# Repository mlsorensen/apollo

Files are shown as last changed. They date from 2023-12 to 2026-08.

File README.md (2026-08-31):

#

This project is archived, see [Apollo2](https://github.com/mlsorensen/Apollo2)

# Apollo for LM Micra/Acaia Lunar

Apollo helps land espresso on your Lunar scale. This project adds brew-by-weight and a small controller 
for La Marzocco Micra with Acaia Lunar. It may also work with other Acaia Bluetooth scales like Pyxis. 

This project is more about scale integration than Micra integration. It cannot do flow profiling or other advanced 
control over the Micra, it is simply collecting data from the scale and acting as a proxy for the paddle switch.

**This is a hobby project, as such there is no support.** It is sort of a hack/proof of concept being beaten into shape.
Contributions are welcome, though this is very much designed to work according to my needs, for customization I'd 
suggest forking and making it your own.

# UPDATES

## Umbra support
I've added support for the Acaia Umbra scale, which is very similar to the Lunar scale, but it lacks a display and onboard
controls. This is ideal for integrations. Aside from being much less expensive. it is a bonus not to have to deal with 
accidentally touching controls. The full blank slab is also nice aesthetically.  Additionally, it has a "sleep" mode. This 
enables Apollo to just connect to the scale when needed, and the scale will go to sleep when disconnected - you don't need 
to touch the scale at all except occasionally to charge or clean it!

To accomodate this I've made one fundamental adjustment. I've comandeered the "target lock" toggle switch to become a 
"connect" button. In over a year I never used this button anyway. When depressed, it will connect to the scale and turn 
on the screen. When disabled it will disconnect and the screen will turn off. For a regular Lunar scale, simply leave the 
toggle depressed and you can continue to manage the system by turning on/off the Lunar as before.

## Horizontal display
This is a part of an effort to build a nicer enclosure, building the device into the top panel of the Micra. All of the
wiring and setup below still applies, with the exception of printing a new top panel and using 8mm push switches in place
of the toggle switch to select target weight.

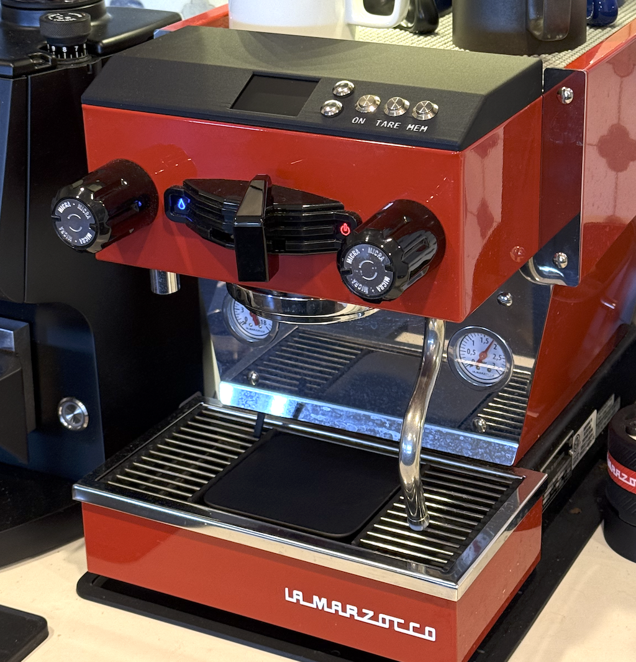
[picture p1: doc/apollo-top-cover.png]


The "Apollo top cover" 3d printing models are in the doc folder.

In my setup I migrated from the Pi Zero 2W to the Raspberry Pi 5, which is overkill CPU-wise and I actually underclock to
1600MHz, but it gives smoother frame rates. I'm sure a Pi 4 or 3 would work too. I use the lite Raspbian image since we 
don't need a full GUI. I insulate the back of the device with tape and tuck it in the open space on the right near the 
steam wand.

I have monitored temperatures closely and not experienced a high enough temperature to throttle the Pi while installed. 
Consider printing the top cover in something more heat resistant like ABS or ASA. I printed in PLA Carbon Fiber for a 
nice texture, rated to withstand 55C, and I've coated the bottom inside shell with a thin layer of neoprene foam. So far 
I haven't seen the top exceed 42C.

I have replaced the top cover screws with M4-0.7 screws made of non-stainless and added 10mm magnets into the top
cover to hold it in place without visible fasteners.

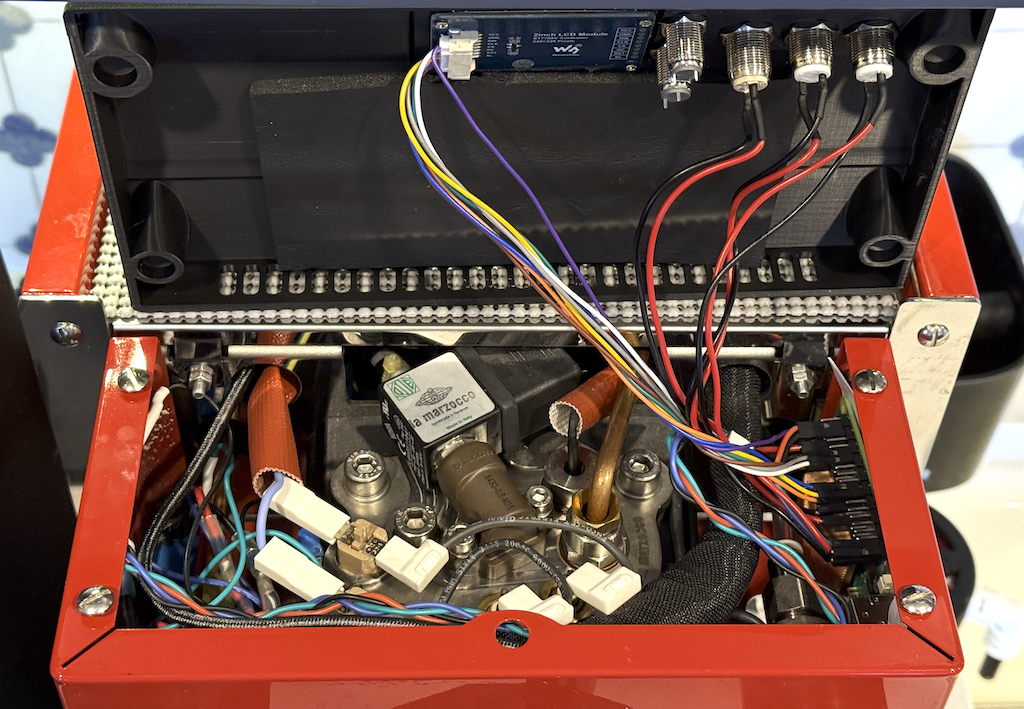
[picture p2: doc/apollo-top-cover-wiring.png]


## Configuration variables
There are some new variables to control framerates and display orientation at `/etc/default/apollo`, documented in the
comments of this file (aka `service/env` in this repo).

## Hardware

### Materials

Note that where external links are provided, they may not age well.

* A Raspberry Pi Zero 2W w/soldered header
* 5v relay w/3.3v compatible logic control
* 5v 2a power supply
* 2.1mm barrel jack connector/wiring harness
* pushbutton switch x 2
* toggle switch
* up/down rocker switch (or two pushbutton switches)
* 2" WaveShare 240x320 SPI display (or compatible)
* Screws - M2.0, M2.5 4mm length, or #3-24 in 1/4" length depending on your 3d printer tolerances
* Silicone 24AWG hook up wire
* Soldering tool and/or 2.54mm crimping set
* 3d printed enclosure, or self-provided alternative

### Controller

A Raspberry Pi was selected to accommodate easy adoption of existing Python libraries without having to
rework them to function on a microcontroller.  Ultimately this is more flexible in terms of expanding
functionality as well.

### Display

The software should support either the [WaveShare 2.0" display](https://www.waveshare.com/2inch-lcd-module.htm) 
or the [2.4" display](https://www.waveshare.com/2.4inch-lcd-module.htm). The 2.4" display seems to have worse
viewing angles and is less sharp, and display_size needs to be updated in `main()`. **For compatibility with the included enclosure, the 2" display should be used.**

### Relay

There isn't one specific relay to link to. Any 5v Arduino/Pi/ESP32 type relay should work. It will have 
common/NC/NO connections on the relay side and 5v/gnd/control pin on the controller side.

### Buttons

I use a momentary pushbutton switch for the tare and memory buttons, a toggle switch for the "scale connect" button,
and an up/down rocker switch for adjusting the target. The up/down rocker switch can be thought of as two momentary
switches with a common ground - you can use two separate buttons as well.

For compatibility with the included 3d printed enclosure, the buttons should be 12mm. The rocker switch should be
rectangular and support 19mm x 13mm opening. 

I found the quality of rocker switches a bit difficult, some had significant bounce leading to them being a bit tricky 
to use. I bought several kinds and used what worked best. The model I ended up using was `MXU1-2-123`.

### Wiring

I bought a crimping tool in order to finish off the connections with standard Dupont 2.54mm connectors for easy
wiring up to the Raspberry Pi header.

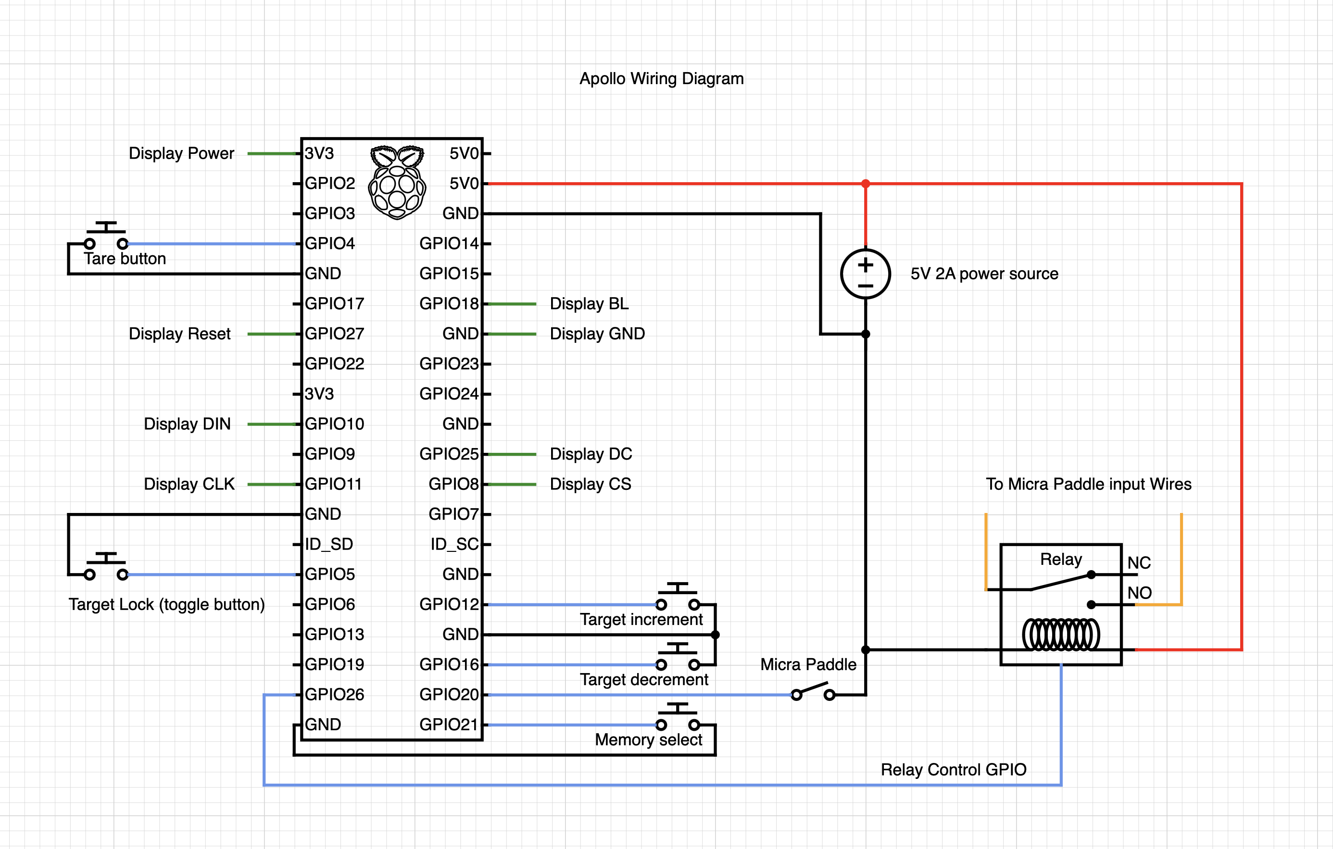
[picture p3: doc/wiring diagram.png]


To simplify the wiring of power and controls between the Micra and the controller, I created a custom harness. This 
keeps the ground and power connections for the relay and switches in the Micra, with just 5v,ground and one wire
per IO going back to the controller (4 pins total).

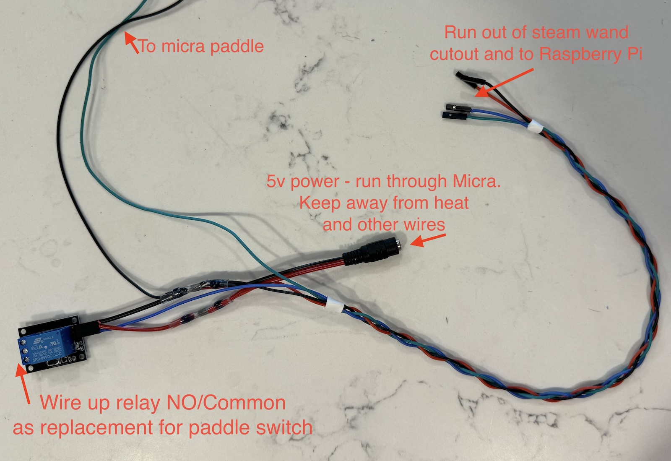
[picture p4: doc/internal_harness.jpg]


The Micra paddle is accessible by removing the top four screws above the group head. Here, you would find a wiring
bundle containing black and white wires connecting to the paddle. These have bullet connectors which can be 
disconnected. You can insert the relay and Pi into this circuit to read the paddle state and control the Micra (or 
perhaps another device).

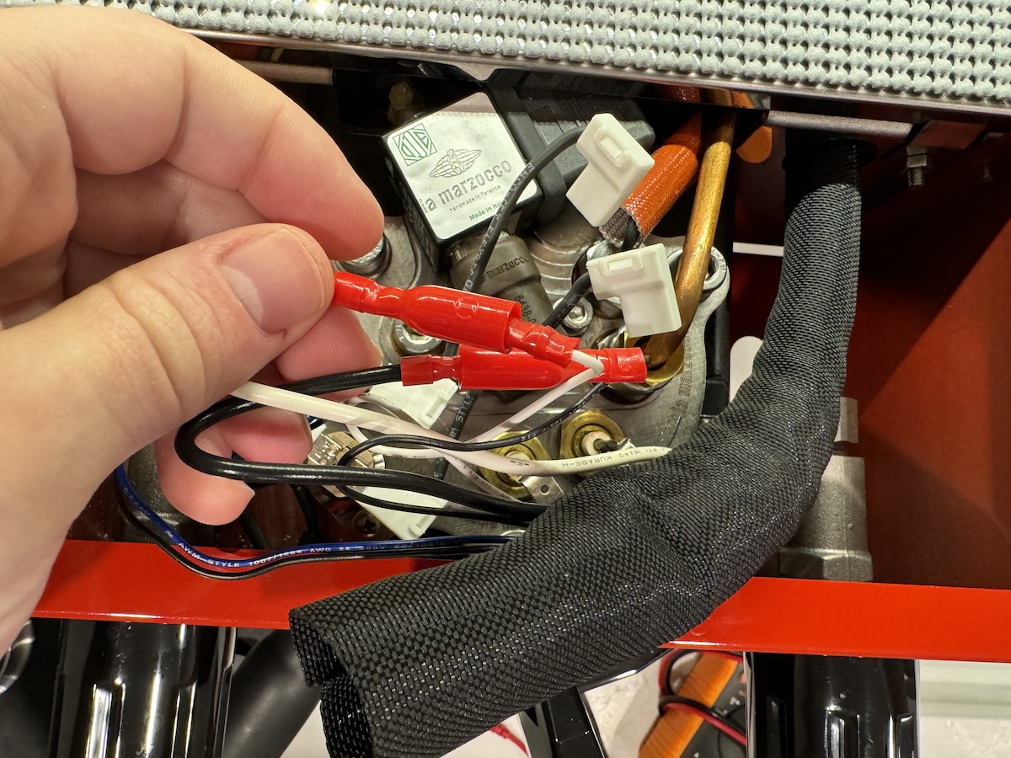
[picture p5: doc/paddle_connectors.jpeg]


### Enclosure

The enclosure STL file can be found [here](doc/Apollo_2inch_v2.stl). It may need fine tuning, depending on the accuracy
and tolerances of your printer.

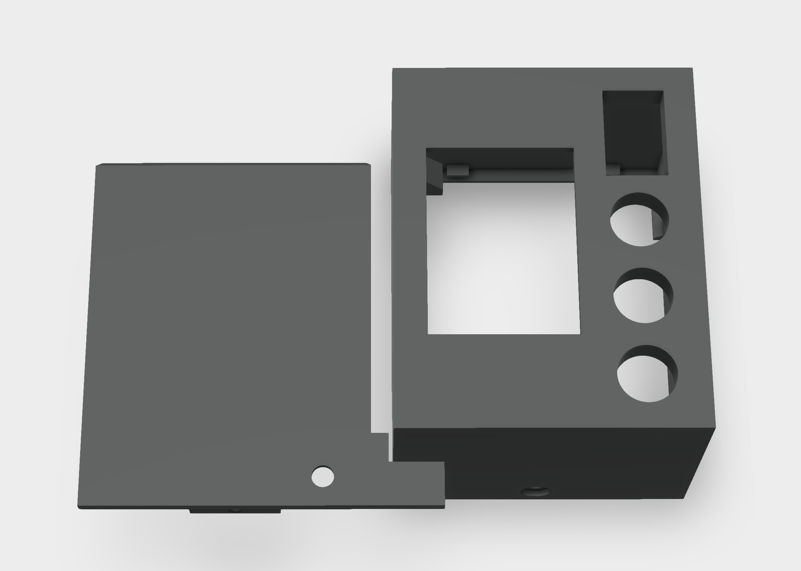
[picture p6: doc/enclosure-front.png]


Looking from the inside, the display mounts with four screws to the far side, along with the buttons.

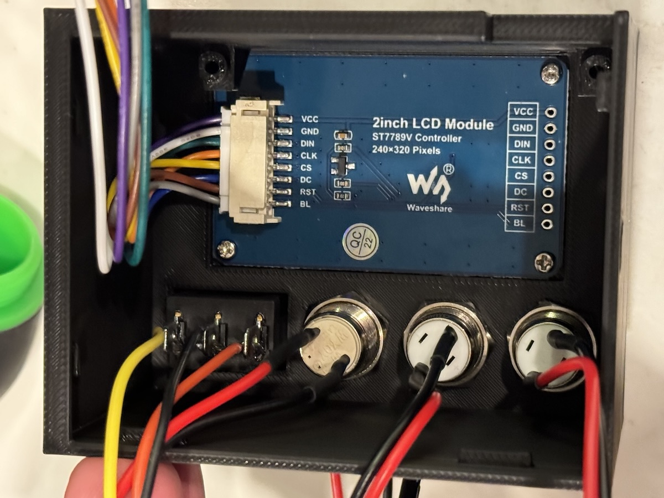
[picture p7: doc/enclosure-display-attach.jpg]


The Raspberry Pi mounts above the display, using the standoffs on the right. There are only two mounts for the Pi. 
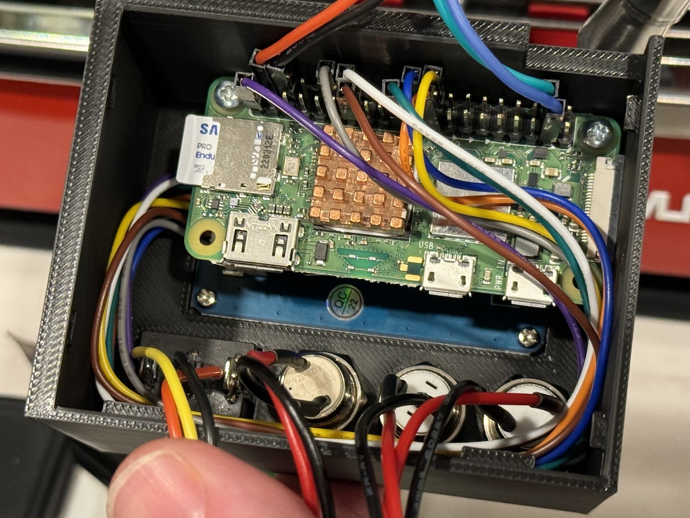
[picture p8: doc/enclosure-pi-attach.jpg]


In all cases be careful not to over-tighten. Ensure everything is connected properly. Route the wiring for the 
paddle/power through the cutout and then up into the group area through the open hole by the steam wand.

The backplate is designed to mount to the Micra on the right of the machine, using the large screw hole. Optional 8mm
magnets can be placed to aid installation and help secure the top of the plate.

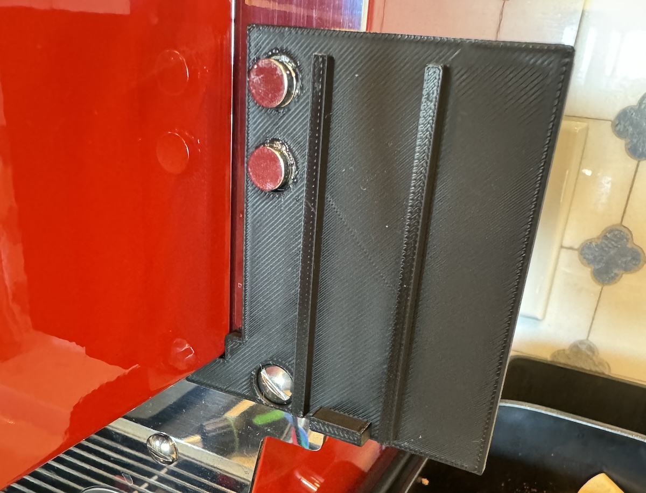
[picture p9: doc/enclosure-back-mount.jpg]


Then the enclosure hangs on the plate from the top clamshell-style. Once hung, a screw can be inserted to fasten the 
bottom of the enclosure to the plate.

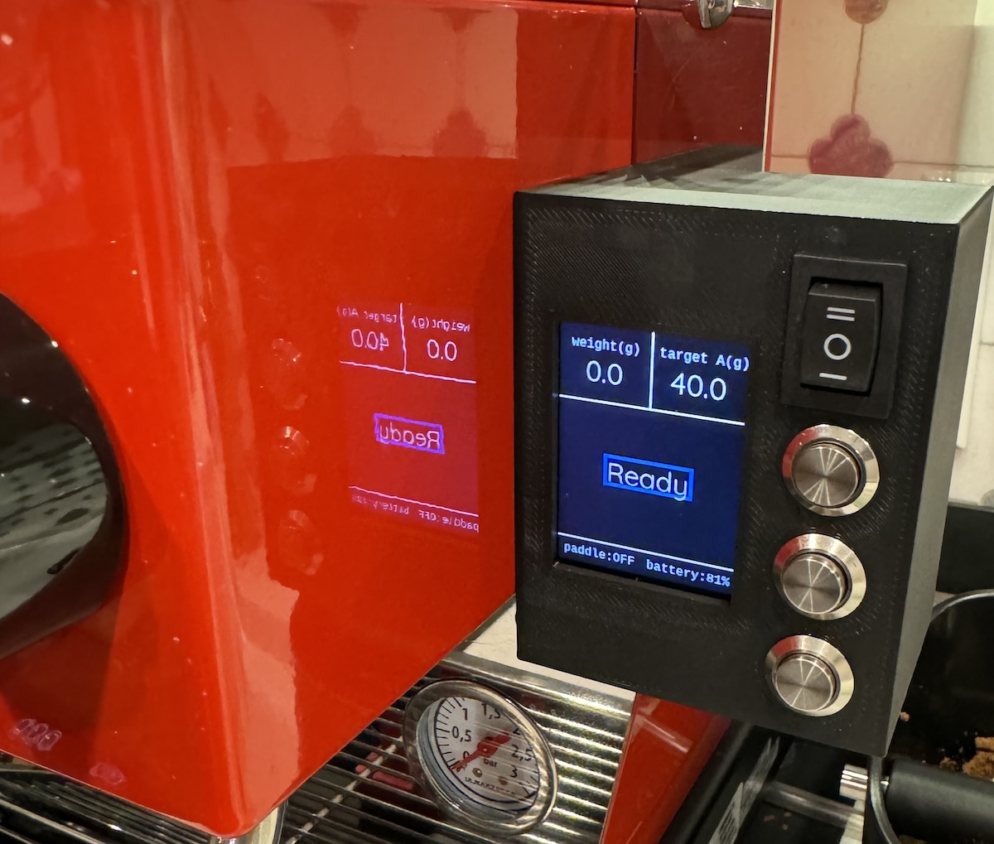
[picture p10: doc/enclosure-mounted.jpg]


## Software Installation

It is assumed you have a Raspberry Pi Debian distribution already installed. As of this writing,
Debian Bullseye is the recommended OS for the Pi Zero 2W. Other versions of Raspberry Pi may also
work.

### Display Driver

The SPI bus must be enabled to drive this display. Log into your Pi and run the following:

```commandline
sudo raspi-config
```
Choose Interfacing Options -> SPI -> Yes  to enable the SPI interface

Next, we want to release memory from the GPU for system use. Still in `raspi-config`, under Performance -> GPU Memory limit 
set to 16M.

Finally, we want to disable the login UI. Under System Options -> Boot / Auto Login choose "Console" 

```commandline
sudo reboot
```

### Software dependencies

```commandline
sudo apt install python3-pandas python3-pip libglib2.0-dev git
sudo pip3 install bluepy
```

#### Apollo Software
TODO: DEB package or install script

```commandline
git clone https://github.com/mlsorensen/apollo.git
cd apollo
sudo mkdir -p /opt/apollo/web
sudo cp -r apollo.py lib /opt/apollo
sudo chmod +x /opt/apollo/apollo.py
sudo cp service/apollo.service /etc/systemd/system
sudo cp service/env /etc/default/apollo
sudo systemctl daemon-reload
sudo systemctl enable --now apollo
```

By default, the software scans for any Lunar device in the vicinity and connects to it. There is no simple
way to set a specific scale MAC address yet.

## Software Development

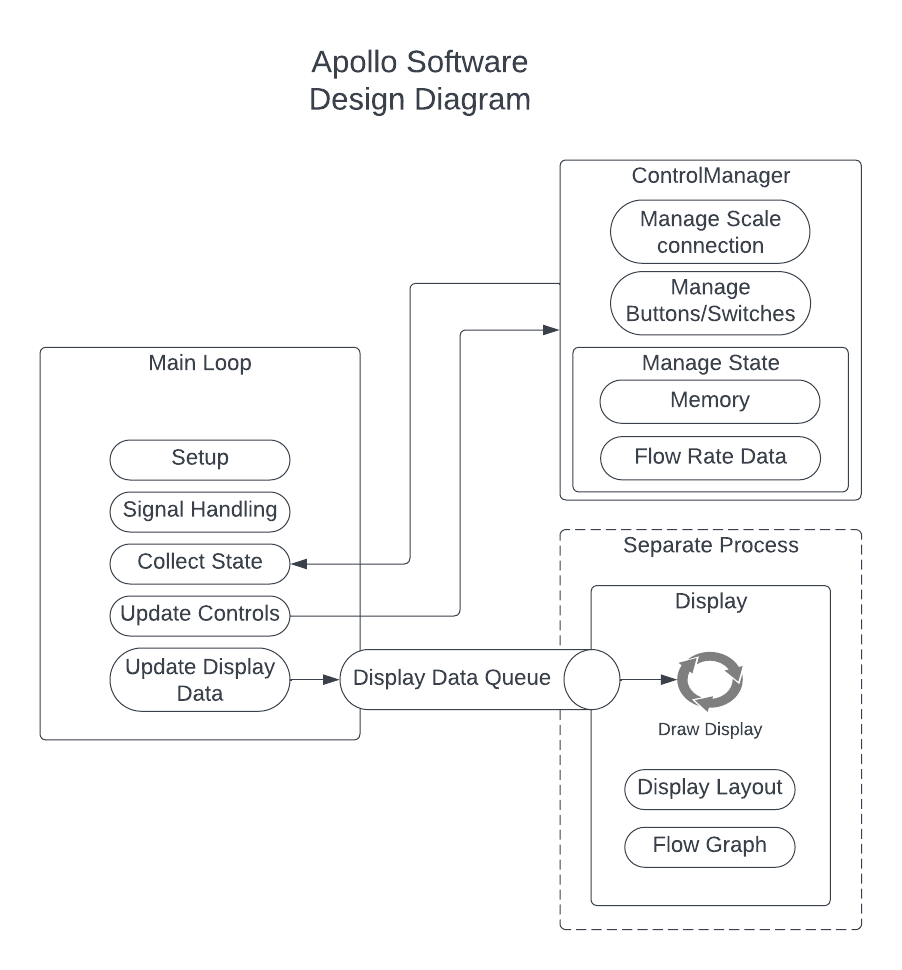
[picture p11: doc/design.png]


### ControlManager

This controls the physical devices. It defines buttons, keeps state, and maintains scale connectivity.

### Display

Display class is responsible for defining how graphics are drawn, and updating the physical display as well as saving
images of finished shots. It runs in a separate process so that display refreshes aren't blocked on anything else. To
achieve this, current data is pushed onto a queue which is constantly read from - the queue is drained on each
refresh and the latest data is displayed.

This was originally using matplotlib, which was CPU intensive and slow. Several other libraries were investigated, but 
they all had their own drawbacks (dependencies), optimization for webpage viewing, performance etc. In the end it was 
decided drawing the graph using simple lines was sufficient and performant.

### Main loop

The main loop is responsible for basic logic of setting up a Display and ControlManager, then orchestrating data
collection and state updates.

### Display

A single frame can be generated using `test_display.py` for design changes to the display. Running `pytest` should be
sufficient to discover this test, run it, and open the resulting image on your workstation.

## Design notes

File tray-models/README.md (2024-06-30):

# Drain Tray Models

This folder contains three models for a recessed Acaia Lunar drip tray on the Micra. This includes a 1/2" NPT
connection that can be plugged with a standard 1/2" fitting if there is no plumbing. 

Your experience with this may vary depending on the quality of your resulting print and your experience in getting 
good results. These are advanced prints due to their size and the need to use higher temperature filament like ABS, ASA, 
or PC. Even with higher temp plastic, avoid shocking the tray with large amounts of boiling water or it can expand and 
crack if layers aren't strongly bonded. Along with the regular tricks for printing ABS, I would recommend printing with 
extra walls (6 or more) to increase strength, particularly around the NPT connection, and to avoid warping.  If your slicer 
supports ironing it is also nice to smooth the surfaces for easier cleaning. Your printer will need to be reliable in
printing supports, both the drip tray and the grille have overhang areas regardless of how they are printed.

There is a built-in tower to hold a float (work in progress).

The scale area is designed with a very slight tilt forward, to promote draining in a way that avoids
touch controls on the Lunar. There are detents to center the scale and keep it from touching the sides
of the recess, which can impact the scale measurements, these are designed to fit the scale without its
adhesive feet.

There is an optional lever that fits on the top left of the grille tray, which will help pop the scale out.

The grille piece comes in two sizes, one that is more flush to the top and one that drops the inside down 8mm. I designed
the recessed version to meet my needs and give me cup clearance for the largest to-go cups I use on occasion. Both will
fit in the same drip tray. These grilles require that you buy 2.5mm stainless rods and cut them to size (60mm and 234mm 
long), snapping them into the tray. I then took my original grille and removed the grille from the frame by taking a
dremel to the six weld points. This frame then snaps into the plastic grille and is friction fit - holds well but is
easily removable. The OEM part for the grille is `C.1.654` in case you want to buy another rather than destroy your 
original. These run about $100 as of now.

The drip tray installation is obvious once you remove the old drip tray from the metal frame. The original is held in
by two snap-ins at the rear that simply need to be pried out of the detents, and the front is attached with double sided 
tape. You can warm the front frame and use a guitar pick or similar to work the adhesive tape free, prying slowly and 
gently with patience.  The printed replacement drip tray just drops in and snaps in the rear, I didn't bother trying to
re-tape it thoroughly in front.

1. Drip tray
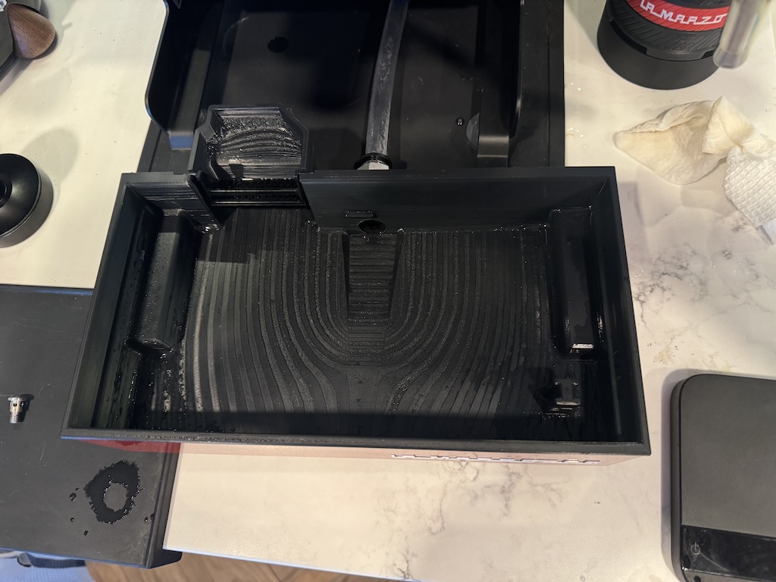
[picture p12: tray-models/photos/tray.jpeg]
   
2. grille with recessed grate/scale (8mm recess)
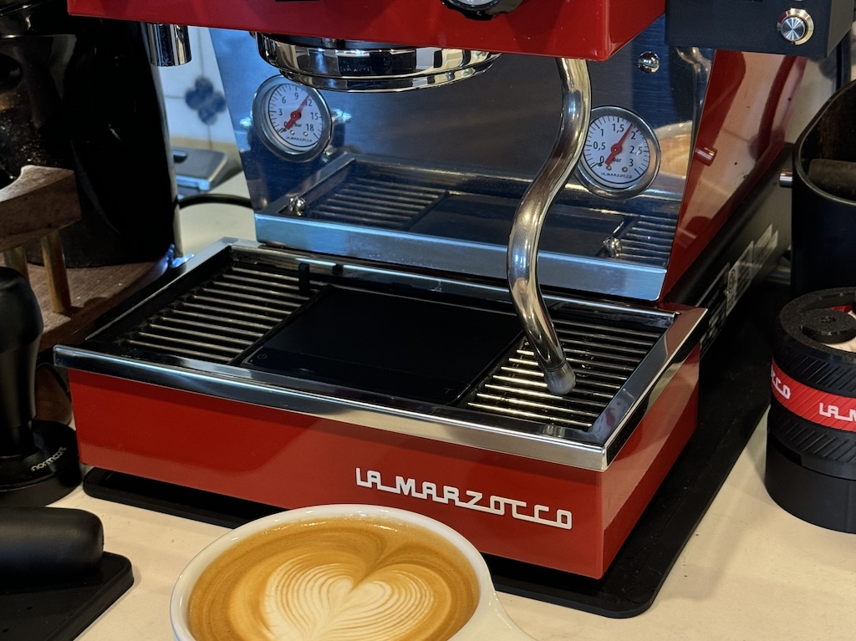
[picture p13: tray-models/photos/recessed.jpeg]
   
3. grille with flush grate/scale
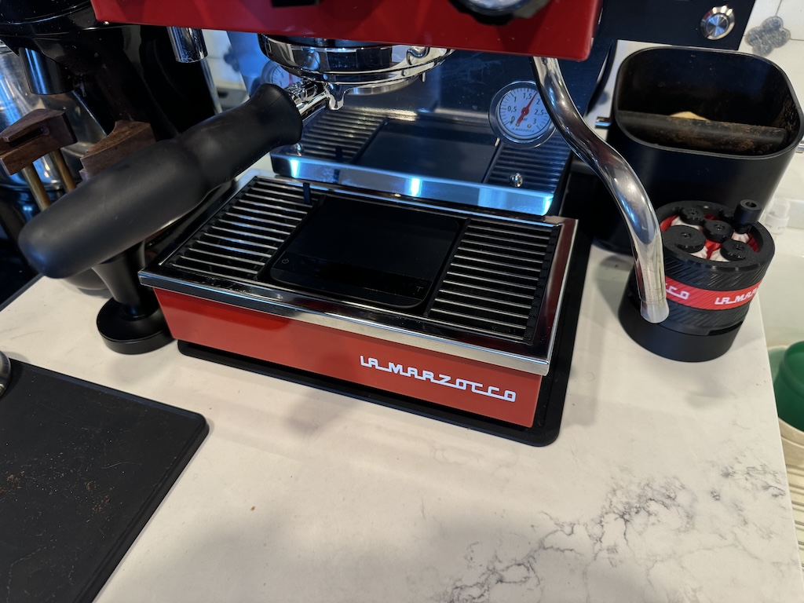
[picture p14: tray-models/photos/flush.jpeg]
   

More photos:

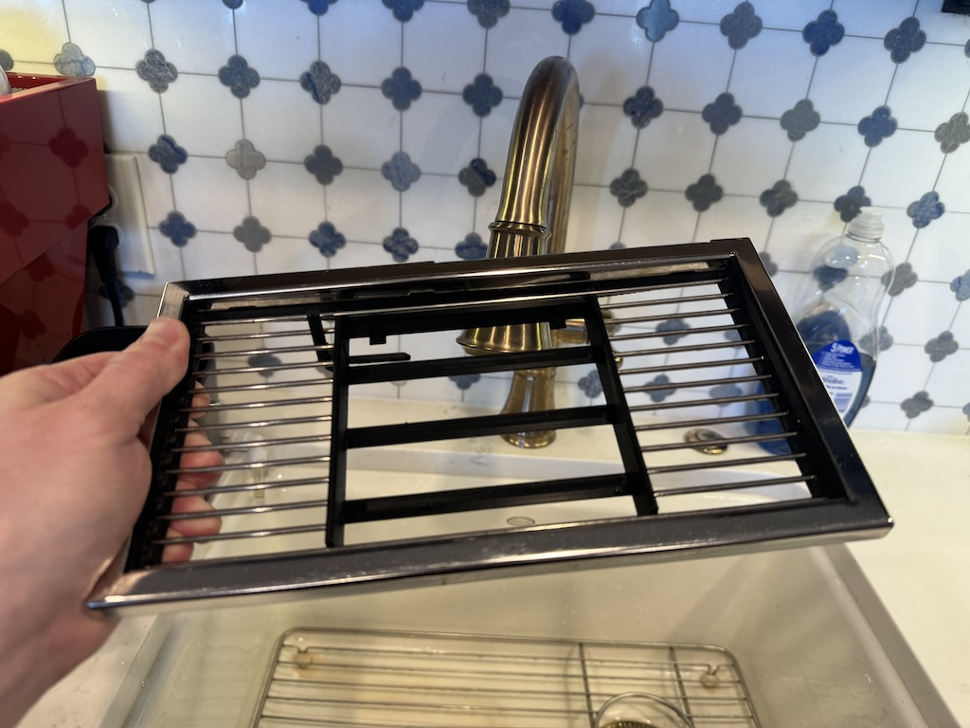
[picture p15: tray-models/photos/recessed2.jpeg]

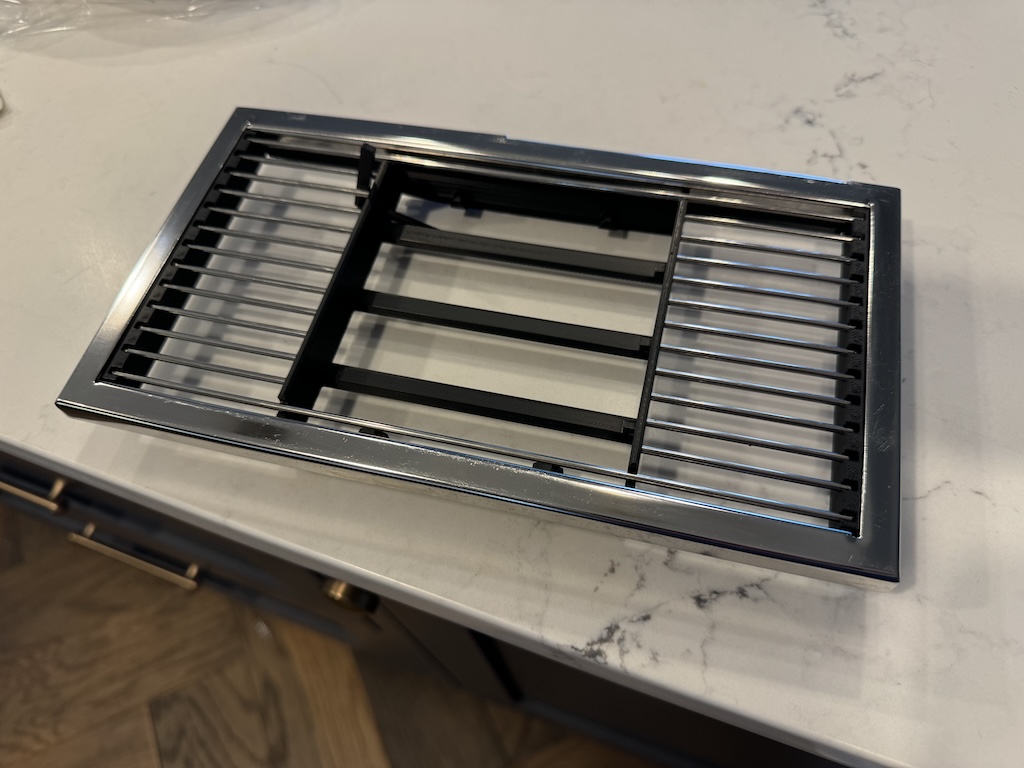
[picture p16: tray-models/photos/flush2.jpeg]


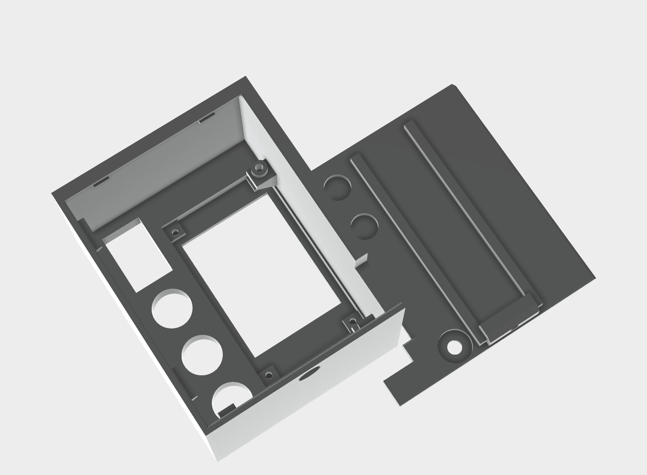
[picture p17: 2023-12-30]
doc/enclosure-back.png

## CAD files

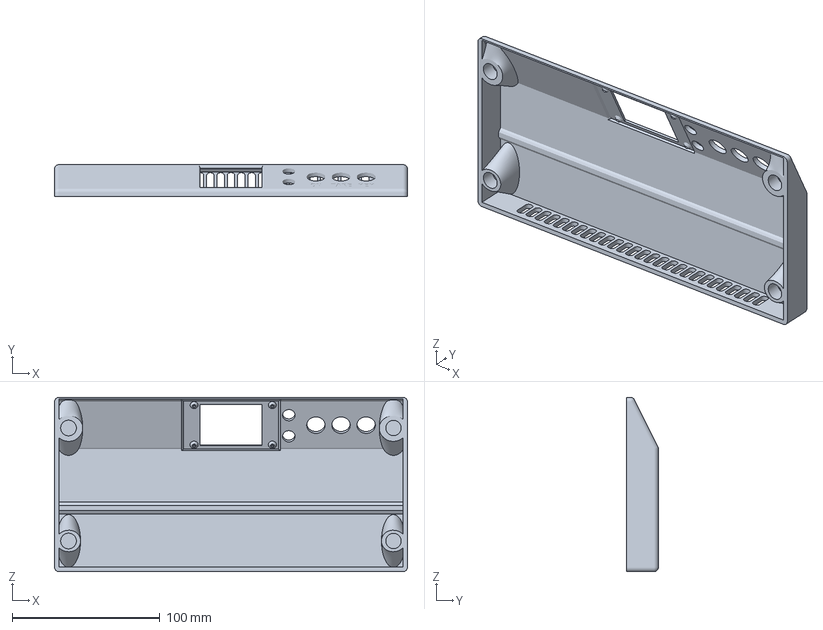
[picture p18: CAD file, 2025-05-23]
doc/Apollo top cover v1.1.3mf
239.0 x 21.5 x 118.0 mm

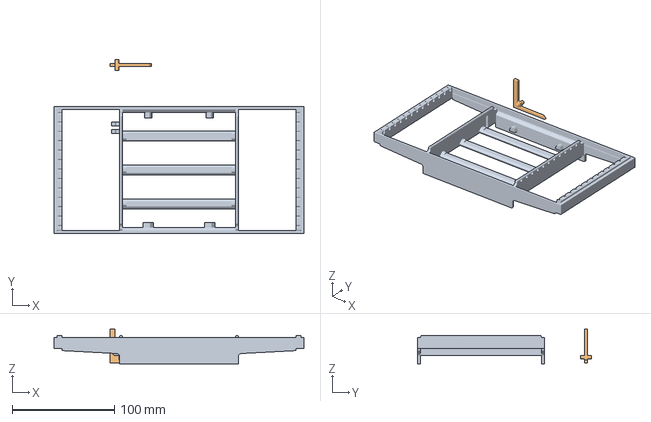
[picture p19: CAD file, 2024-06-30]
tray-models/Micra Tray Grille Flush.3mf
244.0 x 169.9 x 34.0 mm
Body_01_(1)****

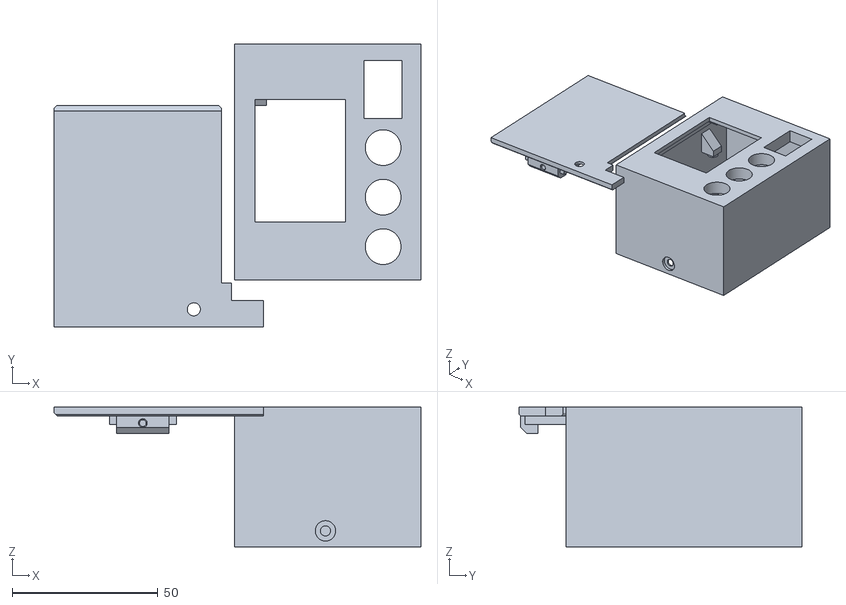
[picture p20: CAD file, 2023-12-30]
doc/Apollo_2inch_v2.stl
126.0 x 97.0 x 48.0

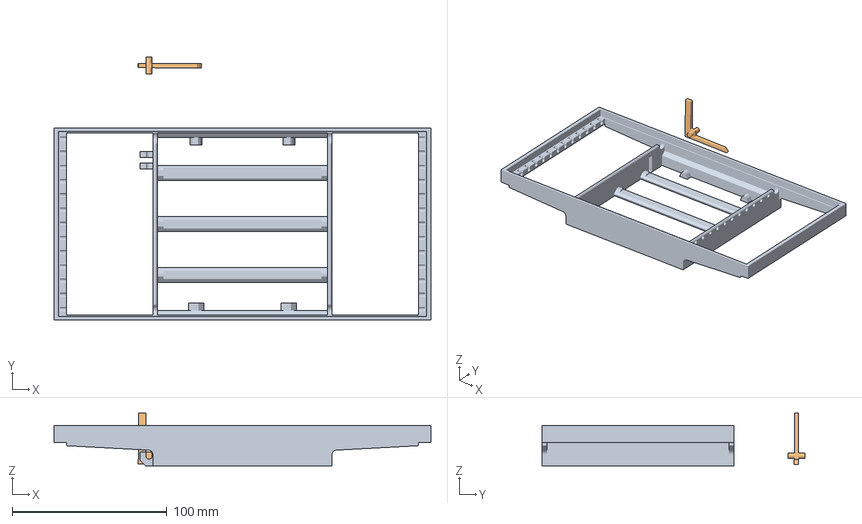
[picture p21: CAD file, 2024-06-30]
tray-models/Micra Tray Grille - extra 8mm.3mf
244.0 x 169.9 x 34.0 mm

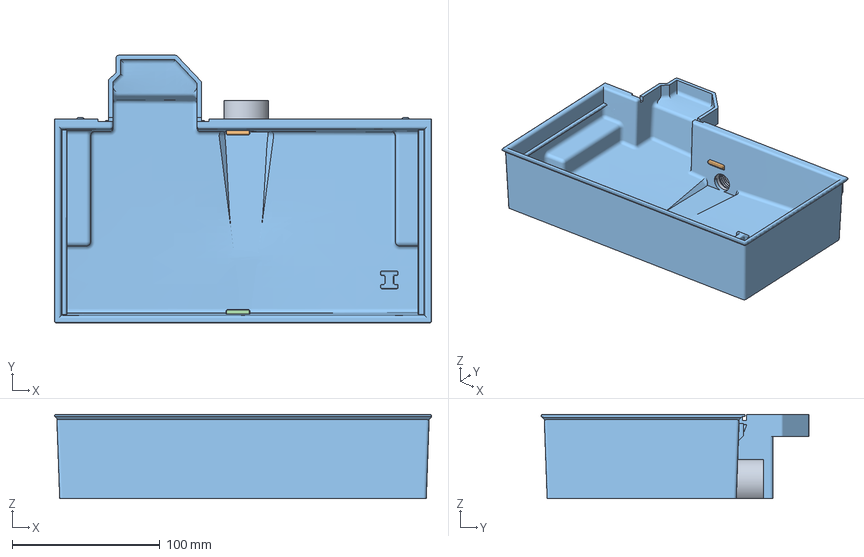
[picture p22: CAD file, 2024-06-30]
tray-models/Micra Drain Tray with half-inch NPT.3mf
255.0 x 181.0 x 57.0 mm

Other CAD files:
tray-models/Micra Drain Tray with half-inch NPT.x_t
tray-models/Micra Tray Grille - extra 8mm.x_t
tray-models/Micra Tray Grille Flush.x_t

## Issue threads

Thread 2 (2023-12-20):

Occasionally don't get weight notifications after connect

mlsorensen, 2023-12-20:
When the pyacaia module connects to the Lunar scale, it sometimes fails to get weight notifications.  Not sure if this is due to the bluetooth stack on the Raspberry Pi, or failure to actually subscribe, or something else. Once we start getting notifications, the functionality is solid, so the immediate workaround is just to reconnect if the weight isn't being updated.

mlsorensen, 2024-08-23:
Calling this fixed after https://github.com/mlsorensen/apollo/commit/899150bd9b79eaa7dcb77105d171d7cfe83ed2da - been running for months with reliable connects on scale power on.

Root cause seems to be that unreliability in bluetooth means we occasionally don't successfully sign up for notifications - simply retry if we aren't getting notified.

Closed 2024-08-23.

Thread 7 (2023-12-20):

Generic scale interface

mlsorensen, 2023-12-20:
Abstract the scale into a class that can have multiple implementations for other Bluetooth scales.  It should have “weight”, “battery” and “connected” values that can be read. Also “tare”, “connect” and “disconnect” functions.

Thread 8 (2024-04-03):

Using only two pushbuttons with new auto tare feature?

msageryd, 2024-04-03:
Thank you for this writeup!
This is relaly cool. I hadn't decided between the Mini and Micra, but your work certainly makes me lean towards the Micra.

I'm currently looking for some nice buttons for this project, and I was wondering if you would you suggest to not implement the tare button now when you have auto tare in software? Or are there other use for the tare button which is not covered by auto tare?

mlsorensen, 2024-08-23:
Yes that's a good point. I still use the tare button when I weigh the beans, and auto tare for the shot of course - but there's still the tare on the scale itself.  I actually considered dropping the button for extra profiles because I found I don't really use it.

Might be worth doing a 2.0 with a slimmed down package and interface. I know there are other projects out there as well now that are more simple and work with multiple machines.

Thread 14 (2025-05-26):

Connection to the paddle

imac941, 2025-05-26:
Hello, unfortunately I don’t know where else to ask this question, so I’m trying here. First of all, thank you very much for the great project. Unfortunately, I don’t know exactly how to wire the paddle. Does anyone happen to have a picture that clearly shows which cable goes to the paddle and how it is connected? Unfortunately, the diagram doesn’t help me. A photo showing the cables would be great. Thank you very much!
Best regards
Flo

imac941, 2025-05-31:
@mlsorensen Thanks for your answer, sorry for the stupid questions. Like this? Or is that wrong?

I currently have it wired like this.
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

Should the cables circled in green be connected to the paddle or to the relay (blue)?
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

I only have problems connecting the paddle, otherwise everything works :)

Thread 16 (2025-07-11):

Blank LCD Screen

creichardt-ie, 2025-07-11:
Hello!

I am looking for someone who got apollo working who could give me a hand (I know there is no support).

I can't get **any** output from apollo on the LCD.

- RaspberyPi5
- 2inch Waveshare LCD display
- Debian GNU/Linux 12 (bookworm) 64bit
- SPI enabled

I know that the display is not broken and correctly connected, since I was able to run the sample from Waveshare "2inch_LCD_test.py" and it outputs on the LCD correctly. Only the display is connected, I did not add the buttons or the rely (I hope that's not the issue).

```
pytest apollo/
=========================================================================== test session starts ================================
platform linux -- Python 3.11.2, pytest-7.2.1, pluggy-1.0.0+repack
rootdir: /home/micra/apollo, configfile: pyproject.toml
collected 2 items

apollo/test_display.py ..
```

In _display.py_ I had to change the path from the font from
label_font = ImageFont.truetype("lib/font/LiberationMono-Regular.ttf", 16)
to
label_font = ImageFont.truetype("/home/micra/apollo/lib/font/LiberationMono-Regular.ttf", 16)

Without changing it to the full path I received an error that the font could not be found/loaded.

Thanks for any hints and tips.
Christian

Update:
I found another project for LCD "https://github.com/joy-it/JoyIT_st7789vw" and I get the sample working with text output on the lcd.

creichardt-ie, 2025-07-11:
With some trial and error, plus adding some logging, I found out that it seems to be related to the scale connection

```
 while not stop:
        if control.try_connect_scale(scale, mgr):
            check_target_disable_relay(scale, mgr)
        if scale is not None and scale.connected:
            (last_sample_time, last_weight) = update_display(scale, mgr, display, last_sample_time, last_weight)
        else:
            display.display_off()
        time.sleep(refreshRate)

```
In the loop it jumps to else.

I don't get any messages/logging from control.py, I am not sure if its even tries to connect to the scale.

creichardt-ie, 2025-07-12:
It works now and if I understand correctly it is because I have no buttons connected.

In apollo.py I made this change to simulate the tare button is there

     #mgr.add_tare_handler(lambda channel: scale.tare())
     mgr.should_scale_connect = lambda: True

I am not a programmer and this simple thing took 3-4 days to figure out :)

Closed 2025-07-12.

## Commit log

2023-12-19 Move flow smoothing algorithm to display module
2023-12-19 Fix flow rate display
2023-12-20 Move live flow rate to graph generation
2023-12-29 Update STL for enclosure
    [Apollo_2inch_v2.stl]
2023-12-30 Update readme, new images of enclosure
    [Apollo_2inch_v2.stl]
2024-06-30 Add tray models, update docs
    [Micra Drain Tray with half-inch NPT.3mf, Micra Drain Tray with half-inch NPT.x_t, Micra Tray Grille - extra 8mm.3mf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]
2025-05-12 feat: repurpose toggle button for scale connection
2025-05-16 feat: add function to render frames that are wide
2025-05-23 chore: add images for top cover
    [Apollo top cover v1.1.3mf]
